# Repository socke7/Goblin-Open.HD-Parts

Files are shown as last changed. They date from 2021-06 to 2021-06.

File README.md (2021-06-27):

# Goblin-Open.HD-Parts
A retractable nose camera setup for Open.HD on a STRIX Goblin

## References
You dont't know what Open.HD is? Read more [here](https://openhd.gitbook.io/open-hd/).<br>
Never heard about the STRIX Goblin? Look [here](https://www.readymaderc.com/products/details/strix-goblin-high-performance-fpv-plank-pnp).<br>
## Credits
This project is based on the nice Goblin nose scan by user billyd60 at [rcgroups](https://www.rcgroups.com/forums/showpost.php?p=46243363&postcount=3574).<br>
## Motivation
Some of the best cameras available at the moment for Open.HD are the Veye IMX290/307/327 MIPI/CSI cameras. They have many useful features for FPV, like WDR and an excellent low light sensitivity - also they come with a high quality lens. A disadvantage is their price, so it was mandatory for me to handle my camera with care. That gave me the idea to make the camera retractable to better protect it in case of crashes or hard landings.
## How it works
This is how it looks from outside:<br>
<br>
Everything is controlled by a simple servo:<br>

## Shopping list
* one of these cameras: [MIPI-CAM-290-ISP](https://www.inno-maker.com/product/mipi-cam-290/), [MIPI-CAM-307-ISP](https://www.inno-maker.com/product/mipi-cam-307/), [MIPI-CAM-327-ISP](https://www.inno-maker.com/product/mipi-cam-327/)
* Raspberry Pi 3A+
* Servo EMAX ES08MAII
* 6 pcs cylinder head screw DIN912 M3x8
* 3 pcs cylinder head screw DIN912 M2x6
* 2 pcs hex nut DIN934 M3
* hex nut DIN934 M2
* 4 ps Nylon hex spacer M2 for mounting the camera - length was 6mm in my case, but may be different for other lenses
* 8 or 12 pcs Nylon hex spacer M2.5 for mounting the Pi
* a stripe of double sided tape for attaching the Pi Mount to the bottom of the fuselage
## Print the parts
Download the stl files from [here](/stl/), I recommend printing the parts with PETG using this settings:
* Nozzle: 0.4mm
* Extrusion Width: 0.5mm
* Layer Height: 0.2mm
* Infill: 30% for NoseMount.stl, other parts 100%
* Support is needed for CameraMount.stl only.
## Assemble
This picture should make clear how to assemble everything:<br>
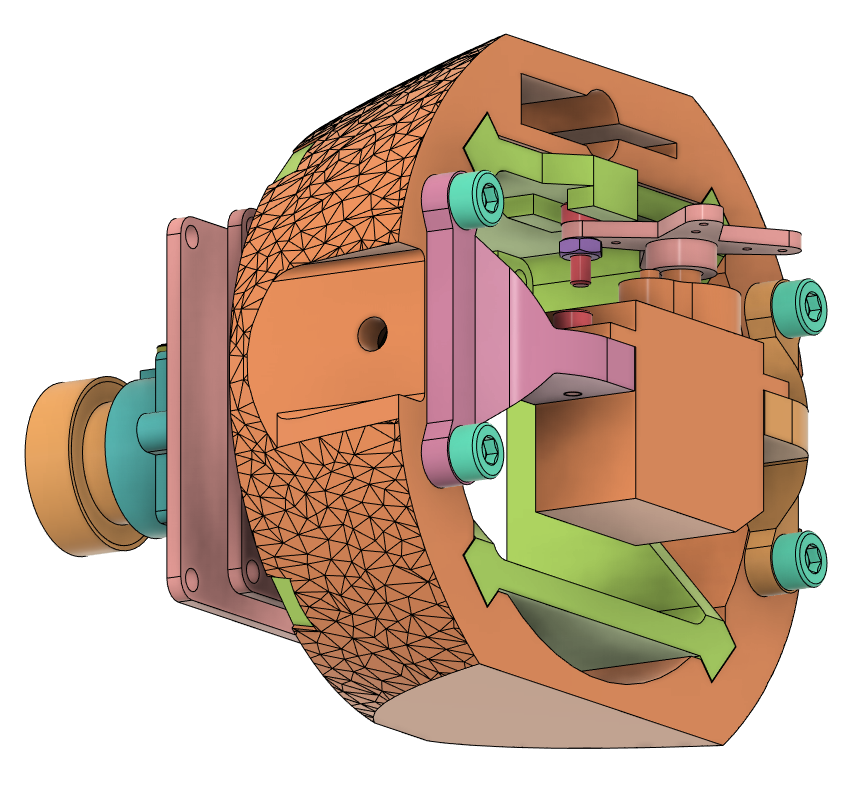
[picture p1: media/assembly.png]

## Integrate
Of course you can control the servo directly from your RC transmitter. But if you have a Flight Controller running Arduplane you could use the [Landing Gear/ Retractable Camera Mount](https://ardupilot.org/plane/docs/common-landing-gear.html) feature!
## Have fun!

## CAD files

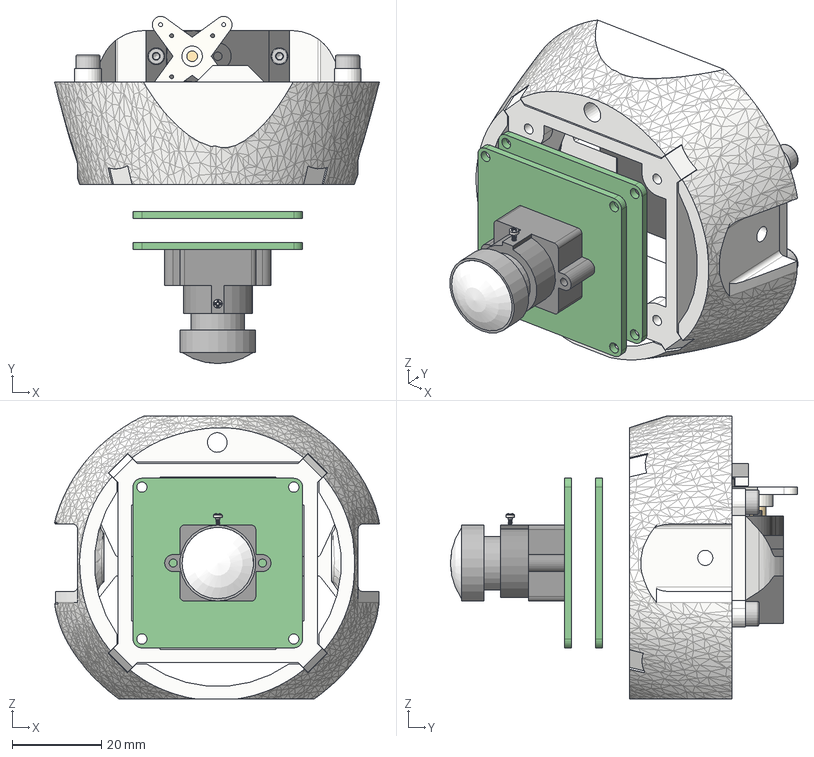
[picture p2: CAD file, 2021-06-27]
step/Goblin Veye Cam Mount ES08 Servo.step
72.8 x 77.8 x 63.3 mm
mount_lens
LENS_Wide_® ã¬®«ç  ¨î
pan head cross recess screw_iso_ISO 7045 - M1 x 4 - Z - 4S
CameraMount
NoseMount
HI_WUERTH 00942 6 cylinder head screw DIN 912 M2x6 A2-70 BLK x 3
ES08 Large Cross
EMAX ES08MxII
_WUERTH 03222 hexagonal nut DIN 934 M2 A2 BLK
HI_WUERTH 00943 8 cylinder head screw DIN 912 M3x8 A2-70 BLK x 4
ServoMountLeftHand
ServoMountRightHand(Spiegeln)

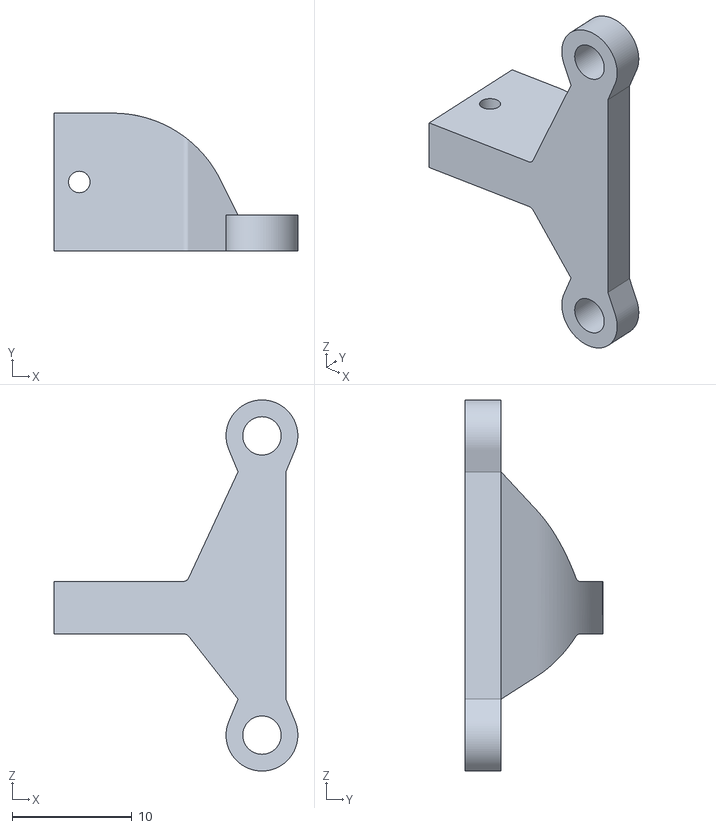
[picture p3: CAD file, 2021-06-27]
stl/ServoMountLeftHand.stl
20.4 x 11.5 x 31.0

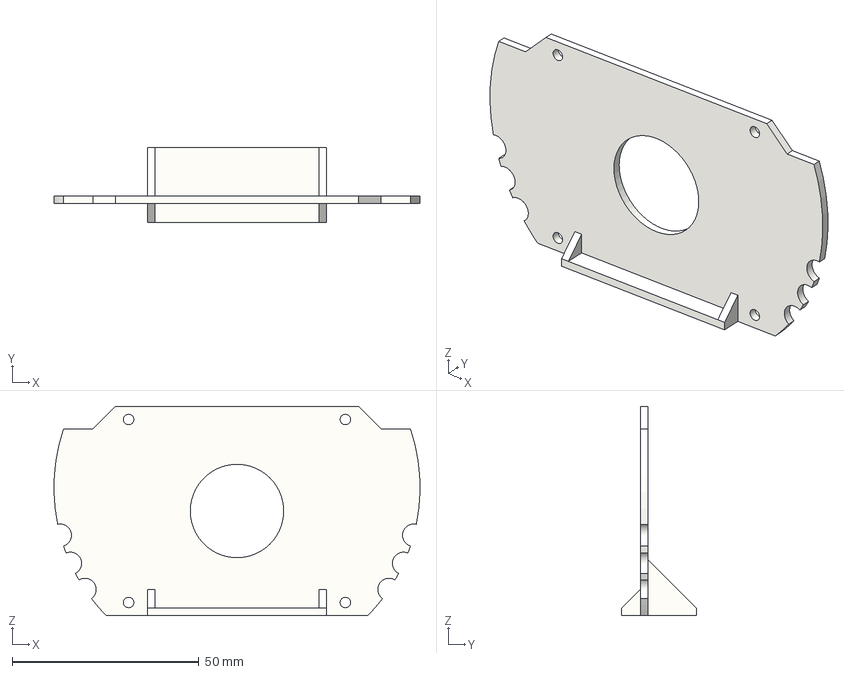
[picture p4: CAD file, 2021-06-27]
step/Pi3A Mount.step
98.0 x 20.0 x 56.0 mm

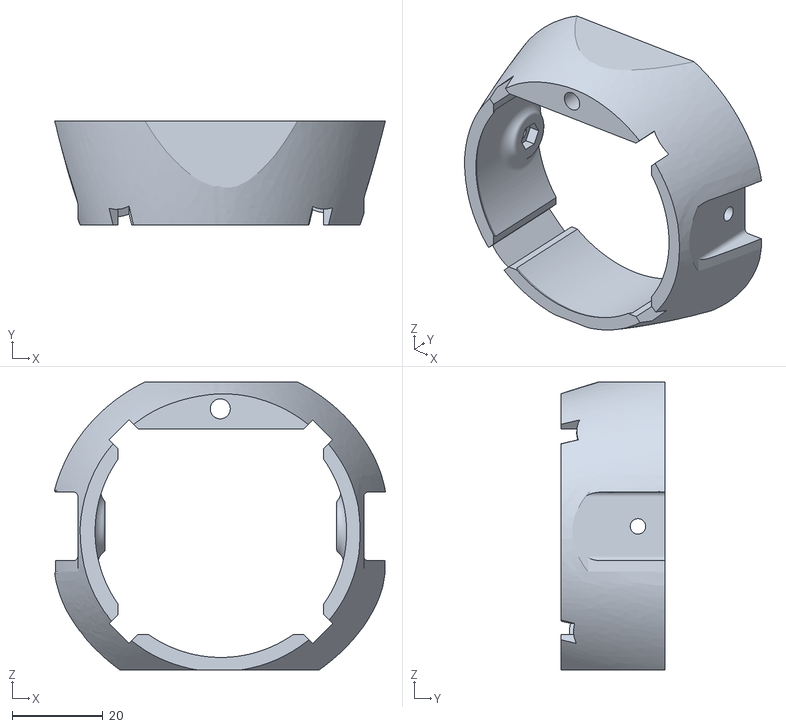
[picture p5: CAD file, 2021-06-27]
stl/NoseMount.stl
72.8 x 23.0 x 63.3

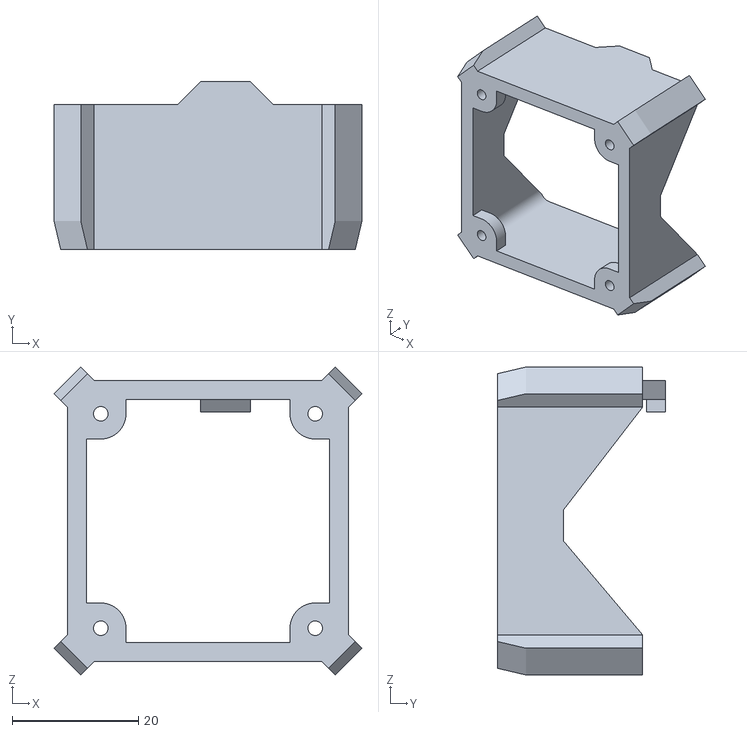
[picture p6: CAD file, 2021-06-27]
stl/CameraMount.stl
48.8 x 26.6 x 48.8

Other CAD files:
stl/ServoMountRightHand.stl
stl/Pi3A Mount.stl
